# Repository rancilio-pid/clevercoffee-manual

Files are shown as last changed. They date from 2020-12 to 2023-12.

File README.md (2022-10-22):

# CleverCoffee Manual

## Über
Dies ist das Handbuch für die Umsetzung des CleverCoffee-Projektes. Dieses Handbuch deckt alle notwendigen Schritte ab. Dazu gehören zum einen die Installation von PlatformIO und das Hochladen auf den Mikrocontroller. Weiterhin beinhaltet das Handbuch die Bestellliste, Infos zum Einbau und der Konfiguration der PID-Parameter.

Hier geht es zum deutschen Handbuch: [Link](https://manual.rancilio-pid.de/de/).

Mehr zum Projekt findet ihr auf der [Clever Coffee Website](http://clevercoffee.de/).

## About

This is the manual for the implementation of the CleverCoffee project. This manual covers all the necessary steps. This includes installing PlatformIO and uploading the code to the microcontroller. The manual also includes the parts list, information on installing and configuring the PID parameters.

Click here for the English manual: [Link](https://manual.rancilio-pid.de/en/)

You can find more about the project on the [Clever Coffee Website](http://clevercoffee.de/).

## Contributing

Bug reports and pull requests are welcome on GitHub at [https://github.com/rancilio-pid/ranciliopid-handbook](https://github.com/rancilio-pid/ranciliopid-handbook).

This project is intended to be a safe, welcoming space for collaboration, and contributors are expected to adhere to the [Contributor Covenant](https://www.contributor-covenant.org/) code of conduct.

### Design and development principles of this manual:

* As few dependencies as possible
* As few (jekyll) customization as possible

## License
This manual is available as open source under the terms of the [MIT License](./LICENSE).

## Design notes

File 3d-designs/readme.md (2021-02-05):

Tipps zum Drucken:

1. Gehäuse auf dem Kopf liegend drucken (um 180° in X oder Y drehen)
2. Ein halbwegs Temperaturstabiles Filament verwenden (normales PLA ist etwas knapp)
3. Optimiert für eine 0,4mm Düse und eine Schichthöhe von 0,2mm
4. Für einen schönen optischen Touch in der ersten Schicht conzentrischen Infill verwenden

Die Magneten mit 6mm Durchmesser (2x 1mm und 1x 2mm dick) mit einem guten Kleber einkleben - Sekundenkleber hat sich als ungeeignet herausgestellt. 

Nach der [Einbauanleitung.pdf](./Einbauanleitung.pdf) zusammenbauen und montieren.

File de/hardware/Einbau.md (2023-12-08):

---
layout: default
title: Einbau
parent: Hardware
grand_parent: DE - Handbuch
has_children: false
nav_order: 3
---

#   {{ page.title }}

<details open markdown="block">
  <summary>
    Inhaltsverzeichnis
  </summary>
  {: .text-delta }
1. TOC
{:toc}
</details>

Grundsätzlich würde ich alle Kabel erstmal mit einer Kabellänge von ca. 60 cm abschneiden. Nach dem Einbau auf Seite 1 und dem Verlegen sollten diese beim Anschließen an Seite 2 gekürzt werden.

Vorbereitung:
* ESP bespielen (ggf. sicherstellen, dass das WLAN funktioniert)
* PCB zusammenlöten (Link zur Anleitung folgt)
* ggf. Blynk einrichten und verbinden
* ggf. Displayhalter drucken / bestellen

Zeitaufwand:
* PID Only ca. 3 h
* Vollaubau weitere 2-3 h

## Zerlegen

Als erstes muss die Maschine zerlegt werden. Hier findet ihr einen [Link zur Demontage](https://clevercoffee.de/rancilio-silvia-demontage/).

## PID only

### Thermostat gegen Temperatursensor tauschen

Kabel (0,14mm2) am Temperatursensor anlöten und mit Schrumpfschlauch versehen. **!!!Unbedingt Pinbelegung beachten!!!** Es empfiehlt sich folgende Belegung zu verwenden:

> Rot = +  
> Schwarz = -  
> Grüne = Signal

Freies Kabelende beschriften

Stecker mit rotem Kabel und Stecker mit grauem Kabel abziehen.

Schrauben 1 + 2 lösen.
Schraube 3 ein wenig lockern.
Das alte Thermostat beiseite legen und aufheben; bereich von der Wärmeleitpaste reinigen.

Bügel mit Schraube, Beilagscheiben und Muttern vorbereiten. Bügel wieder einbauen dabei Schraube 3 und 2 festziehen, 1 noch etwas locker lassen.

Die neue Schraube mit Hilfe der zwei Muttern so einstellen, dass die Schraube auf dem Temperatursensor aufliegt. Muttern festziehen.
Temperatursensor auf der Unterseite mit etwas Wärmeleitpaste versehen, unter der neuen Schraube platzieren und Schraube 1 anziehen. Der Bügel sollte sich dabei leicht verformen. So wird sichergestellt, dass der Sensor fest sitzt, aber nicht zu sehr gequetscht wird.  

### Stromversorgung

1,5mm2 Kabel blau mit Flachsteckhülse mit Abzweig versehen und in den abgezogenen Stecker mit Rotem Kabel stecken.
Ein weiteres 1,5mm2 Kabel blau mit Flachstecker versehen und ebenfalls einstecken. Alles mit einem Schrumpfschlauch versehen.
Kabel eins geht zum SSR der Heizung, Kabel zwei zum Netzteil. Welches Kabel dabei wofür verwendet wird ist egal.

1,5mm2 Kabel schwarz mit Flachsteckhülse mit Abzweig versehen. Den unteren Stecke am Schutzschalter abziehen, auf den Abzweig stecken und beides direkt wieder anstecken.

Kabel sinnvoll verlegen und einen Platz für das Netzteil festlegen. Kabel vor dem anschließen entsprechend kürzen.

Wenn man das Netzteil aus der Bestellliste nimmt, verbindet man Eingang N blau mit blau und Eingang L schwarz mit braun.
Der Ausgang von Netzteil schwarz-rot kommt dann auf den V_IN 5V Eingang am PCB.

### SSR Relais Heizung

Montagepunkt für das SSR festlegen. Es kann bei der Rancilio Silvia E z.B. über der "CPU" neben dem Wasserschlauch mit doppelseitigem Klebeband angebracht werden. Alternativ befindet sich eine Schraube an der Vorderseite der Maschine (hinter der Abdeckung), auf die das SSR mit einer Mutter festgeschraubt werden kann.

An Kabel 2 (blau) des Schrittes oben, eine Ringöse pressen (Kabel vor dem Anschließen entsprechend kürzen) und an einen beliebigen Pol des SSR-Ausgangs anschließen.
Ein weiteres Kabel 1,5 mm2 mit einer Ringöse versehen und am zweiten Pol des SSR-Ausgangs befestigen. Kabel zum Stecker mit dem grauen Kabel verlegen, welches ursprünglich am Thermostat war und entsprechend kürzen. Einen Flachstecker aufpressen und anschließend mit einem Schrumpfschlauch versehen.

Zwei Kabel (rot und schwarz) an der Eingangsseite des SSR anschließen. Ich habe dafür 0,5 mm2 Kabel verwendet und ebenfals Ringösen aufgepresst. Es können aber auch die 0,14 mm2 Kabel mit Aderendhülsen o.ä. verwendet werden.
Freie Kabelenden beschriften und richtung 3-Wegeventil legen.

### Einbau des Controllers

Der Microcontroller (ESP) sollte auf das von uns bereitsgestellte Adapterboard (PCB) gesteckt werden. Dieses kommt mit Klebefüßen, so dass es an einer beliebigen günstigen Position befestigt werden kann, an der die Kabel zusammenlaufen. Dies kann im hinteren oder vorderen Teil der Maschine sein, je nach Modell.

## Vollausbau

**Wichtig!: Beim anschließen des Brühschalters bitte unbedingt den Hinweis im Schaltplan zur Trennung von 230V und 3.3/5V am Schalter beachten.** (Wer der Anleitung unten folgt, muss nichts "zusätzlich" beachten.)

### Silvia (v2)

Beim Vollausbau werden sowohl Kaffebezug (inklusive 3-Wege-Ventil) und Dampfbezug über den ESP gesteuert. 
Dazu gibt es grob drei Arbeitsschritte, die unten genauer ausgeführt werden.
1. Schalter auf LED umrüsten
2. Pumpe anschließen
3. Magnetventil anschließen

#### Schalter Umrüsten

Es müssen sowohl der Schalter für Kaffebezug als auch für den Dampf auf LED umgerüstet werden. 
Dazu dieser Anleitung folgen: [LED-Umbau der Schalter](LED_Umbau.md)

Da direkt beide Schalter umgebaut werden, bietet es sich an, je ein gemeinsames Kabel für 3.3V und GND zu ziehen und dieses vom ersten zum zweiten Schalter durchzuschleifen. Inklusive der beiden Signalleitungen braucht es dann nur vier statt sechs Kabel quer durch die Maschine. 

#### Magnetventil anschließen 

1. Vom Hauptschalter L (schwarz) ein Kabel zum Relais für Pumpe und Ventil ziehen. Dieses Kabel werden sich Pumpe und Ventil teilen. Am Ende beim Relais also z.B. eine Wago-Klemme für drei Kabel oder einen Steckverbinder mit Abzweig anbringen. 
2. Weiteres (kurzes) Kabel von Wago/Steckverbinder zu "SW1" auf der 220V-Seite des Relais legen. 
3. Am zweiten Anschluss von SW1 am Relais ein Kabel anschließen. Kabel so ablängen, dass es zum Ventil führt. Steckverbinder anbringen, orangenes Kabel am Ventil abziehen, stattdessen neues Kabel aufstecken. 
4. Weiteres Kabel N (rot) zum Ventil legen und auf den Stecker mit vormals weißem Kabel aufstecken. Ich habe den Strom beim neuen Netzteil für den ESP abgegriffen, im Prinzip eignet sich aber jedes in der Nähe liegende Kabel mit N (rot) vom Hauptschalter. 
5. Kabel für 5V, GND und VALVE vom ESP zum Relais legen. (Wenn Dupont-Stecker am ESP verwendet werden, bietet es sich an, direkt auch die Leitung für das Pumpen-Signal mit anzubringen). Am Relais darauf achten, dass das die Steuersignal korrekt anliegen (wenn Ventil wie oben an SW1 angeschlossen, dann Signal für Ventil an CH1). 
6. Software konfigurieren, flashen, Maschine mit dem Strom verbinden, Bezug testen -- das Ventil sollte deutlich hörbar klacken, wenn der Bezugschalter umgelegt wird. 
7. Vor dem Weitermachen Maschine vom Strom trennen.

#### Pumpe anschließen

1. Ein zweites (kurzes) Kabel von Wago/Steckverbinder aus Schritt 1 des Ventil-Anschlusses zu "SW2" auf der 220V-Seite des Relais legen. 
3. Am zweiten Anschluss von SW2 am Relais ein Kabel anschließen. Kabel so ablängen, dass es zur Pumpe führt und einen Steckverbinder mit Abzweig anbringen. Das weiße Kabel an der Pumpe abziehen, auf den Abzweig des neuen Kabels stecken, und gemeinsam wieder an der Pumpe anbringen. 
4. Wenn nicht beim Anschluss des Ventils schon erledigt, Kabel für das Steuersignal der Pumpe vom ESP zum Relais legen (wenn Pumpe wie hier beschrieben an SW2 angeschlossen, dann Signal für Pumpe an CH2). 
5. Maschine an Strom anschließen, Bezug testen. 
5.1. Wenn alles funktioniert: Glückwunsch, Vollausbau abgeschlossen! 
5.2. Wenn die Pumpe nichts tut: Vermutlich schaltet dein Relais nur beim Nulldurchgang (mehr Info hier: [Bestellliste](../bestellliste.md)). Um das zu testen, einen 100k Ohm Widerstand (Leistung 1 Watt, bitte weitere Hinweise in der Bestellliste beachten) parallel zur Pumpe anschließen. Ich habe dazu beide Kabel an der Pumpe abgezogen und die Stecker abgeknippst. Dann neue Stecker anbringen und dabei zusätzlich zum Kabel jeweils ein Beinchen des Widerstands mit verpressen. Danach müssen die Kabel vorsichtig (und gemeinsam) angebracht bzw. abgenommen werden, da sie jetzt durch den Widerstand verbunden sind. Zum Abschluss noch einmal Bezug testen und den Vollausbau genießen! 

## Display

Es gibt unzählig viele Möglichkeiten das Display zu positionieren. Folgend könnt ihr zwei Beispiele sehen:

Displayhalterung | Powered by Dremel
:---:|:---:
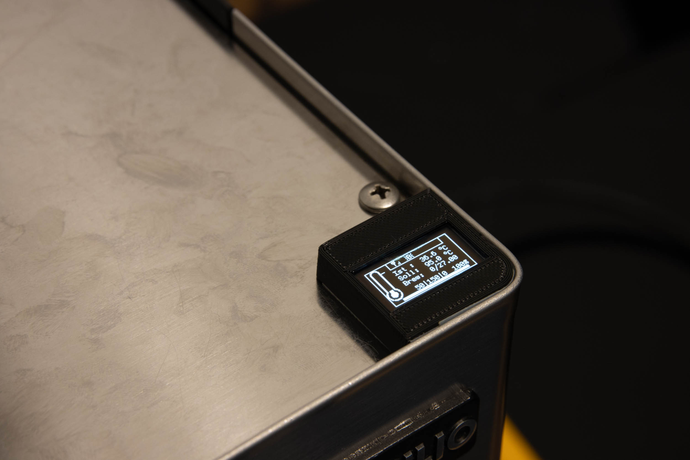
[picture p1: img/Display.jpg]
Display
|

Wer einen Dremel besitzt, etwas Geschick mitbringt und kein Problem damit hat, dass Änderungen irreversibel sind, kann damit eine sehr saubere und solide Lösung ausarbeiten.

Wer hintgegen eine reversible Lösung sucht muss sich um eine Displayhalterung (aka 3D Case) bemühen. Eine "Standardlösung" ist aktuell nicht bekannt, aber für alle 3D-Drucker Besitzer, liegen entsprechende Vorlagen auf [Github](https://github.com/rancilio-pid/ranciliopid-handbook/tree/main/3d-designs) (inkl. [Anleitung](https://github.com/rancilio-pid/ranciliopid-handbook/blob/main/3d-designs/Einbauanleitung.pdf) für den Einbau und die Magnete):

* [Rancilio STL](https://github.com/rancilio-pid/ranciliopid-handbook/blob/main/3d-designs/Case%20Rancilio.stl){:target="_blank"}
* [Gaggia STL](https://github.com/rancilio-pid/ranciliopid-handbook/blob/main/3d-designs/Case%20Gaggia.stl){:target="_blank"}
* [Universal-Halter](https://www.thingiverse.com/thing:4897546){:target="_blank"}
* [Halterung zum reinklicken](https://www.thingiverse.com/thing:4662947){:target="_blank"}

## Spannende Addons die gleich mit erledigt werden können

* Senkschraube am Sieb
* Reinigung der Wasserschläuche (sofern die Maschine nicht neu ist)
* [LED-Umbau der Schalter](LED_Umbau.md)

## Ausblick

Features die ebenfalls eingebaut werden können:

* digitales Manometer
* [integrierte Waage](Waage.md)
* Silvia E Zeit für automatisches Ausschalten verändern
* Automatische Funktion zum Wechsel von Dampf auf Brühen

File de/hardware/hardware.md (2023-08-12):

---
layout: default
title: Aufbau
parent: Hardware
grand_parent: DE - Handbuch
has_children: false
nav_order: 1
---

# Aufbau und Einbau der Hardware
{: .no_toc }

Inhaltsverzeichnis

* TOC
{:toc}

## Trockenaufbau

Wenn ihr die einzelnen Komponenten beisammenhabt, startet ihr am besten mit einem Trockenaufbau außerhalb eurer Maschine. So könnt ihr das System zum Laufen bringen und kommt jederzeit problemlos an alle Stecker etc. heran.

Die Heizung eurer Maschine könnt ihr z. B. mit einer Glühbirne simulieren, jeder andere 230V Verbraucher tut es aber genauso gut.

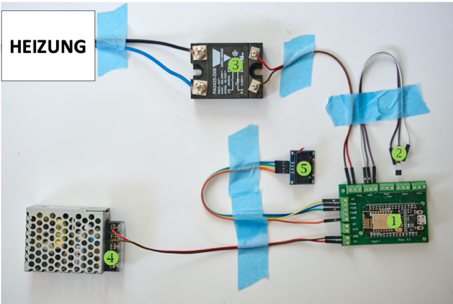
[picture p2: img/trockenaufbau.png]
Trockenaufbau


*(1=Mikrocontroller, 2=Temperatursensor, 3=SSR Relais für Heizung, 4=Schaltnetzteil, 5=Display)*

Das PCB für den (neuern) Mikrocontroller ESP32 sieht wie folgt aus:
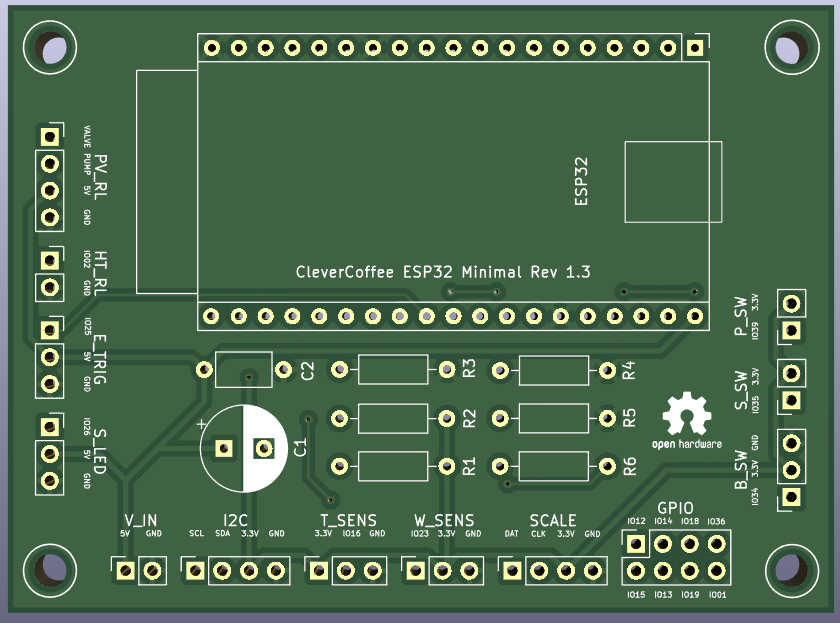
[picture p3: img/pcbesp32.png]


Das PCB für den (älteren) Mikrocontroller ESP8266 sieht wie folgt aus:

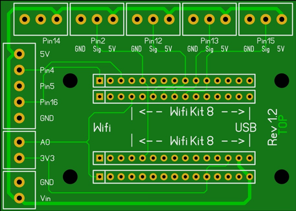
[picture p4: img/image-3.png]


##  PIN Belegung vom PCB ESP32

PIN Software | Bezeichnung auf dem PCB | Belegung
-|-|-
PIN 2 | HT_RL | SSR Heizung     
PIN 16 | T_SENS | Temperatursensor
PIN 21 | IC2 (SDA) | Display-PIN SDA
PIN 22 | IC2 (SDL) | Display-PIN SCL
GND/Vin | V_IN | Netzteil (5Volt)
PIN 17 | PV_RL (Valve) | Relais Ansteuerung Magnetventil
PIN 27 | PV_RL (Pump) | Relais Ansteuerung Pumpe
PIN 34 | B_SW | Bezugsschalter oder Optokopler 
PIN 35 | S_SW | Dampfschalter
PIN 39 | P_SW | Powerschalter (aktuell nicht in Software enthalten)
PIN 25 | E_TRIG | Anschluss Trigger Silvia E CPU
PIN 26 | S_LED | Status oder Temp LED
PIN 23 | W_SENS | Wasserstandssensor
PIN 32 | SCALE (DAT) | Waage DAT
PIN 33 | SCALE (CLK) | Waage CLK

##  PIN Belegung vom PCB ESP8266

Die einzelnen Komponenten werden wie folgt angeschlossen:

PIN | Belegung
-|-
PIN 14 | SSR Heizung     
PIN 2 | Temperatursensor
PIN 4 | Display-PIN SDA
PIN 5 | Display-PIN SCL
GND/Vin | Netzteil

### Vollausbau

Bei dem „Vollausbau“ wird noch die Steuerung für Magnetventil und Pumpe benötigt:

PIN | Belegung
-|-
PIN 12 | Relais Ansteuerung Magnetventil
PIN 13 | Relais Ansteuerung Pumpe

## Einbau

### Temperatursensor anschließen

**ACHTUNG!!** Aktuell kann es sein, dass der TSIC mit einem falschen Datenblatt ausgeliefert wird. Hier wird die Polung falsch angegeben.
Lest hierzu bitte folgenden Thread im Chat durch: [Link](https://chat.rancilio-pid.de/ranciliopid/pl/dcf38jzk3pnoig5hi64nuodeqc).

Besondere Sorgfalt müsst ihr bitte beim Anschließen des Temperatursensors TSIC 306 walten lassen: sobald dieser einmal falsch angeschlossen Spannung bekommen hat, ist er entweder sofort zerstört oder zumindest vorgeschädigt und liefert dadurch fehlerhafte Messwerte. Daher ist es immer ratsam einen Ersatz-Sensor parat zu haben.

* Sensor V+ : Board PIN 2 5V
* Sensor Signal: Board PIN 2 Signal
* Sensor GND:  Board PIN 2 GND

Wie ihr zu der Beschreibung zum Board sehen könnt, muss an Pin 2 der Temperatursensor angeschlossen werden. Die oberen Ports (14, 2, 12, 13, 15) sind einheitlich jeweils von links nach rechts mit Minus(-), Signal, 5V(+) belegt.

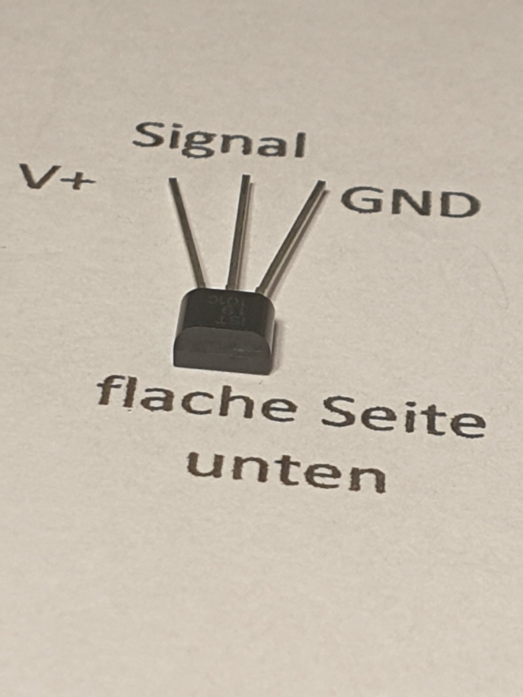
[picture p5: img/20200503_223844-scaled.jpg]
TSIC Sensor


Da wir öfters hören, dass die mitgelieferte Bildbeschreibung des TSIC nicht gut ist, haben wir hier nochmals die Pins vom Sensor dargestellt. Die flache Seite liegt unten. Ein falsch gepolter TSIC sollte entsorgt werden! Er misst vermeintlich richtig, aber definitiv nicht mehr genau.

Beim Anschließen des SSR zur Ansteuerung der Heizung ist es wichtig, dass die Polarität der SSR-Ports 3 und 4 beachtet werden:

* SSR Port 3 (+) : Board PIN 14 Signal
* SSR Port 4 (-) : Board PIN 14 GND

Damit habt ihr das System zum ersten Mal aufgebaut.

### PIN Belegung vom PCB

Pin|Funktion
-|-
Pin 12| Relay für das Ventil
Pin 13| Relay für die Pumpe
Pin 15| Schalter Brühtaste
Pin 14| Relay für die Heizung
Pin 2| Temperatursensor
A0| Drucksensor
|
Pin 4| SDA
Pin 5| SCL
Pin 16| E-Trigger Standby Trigger Silvia E

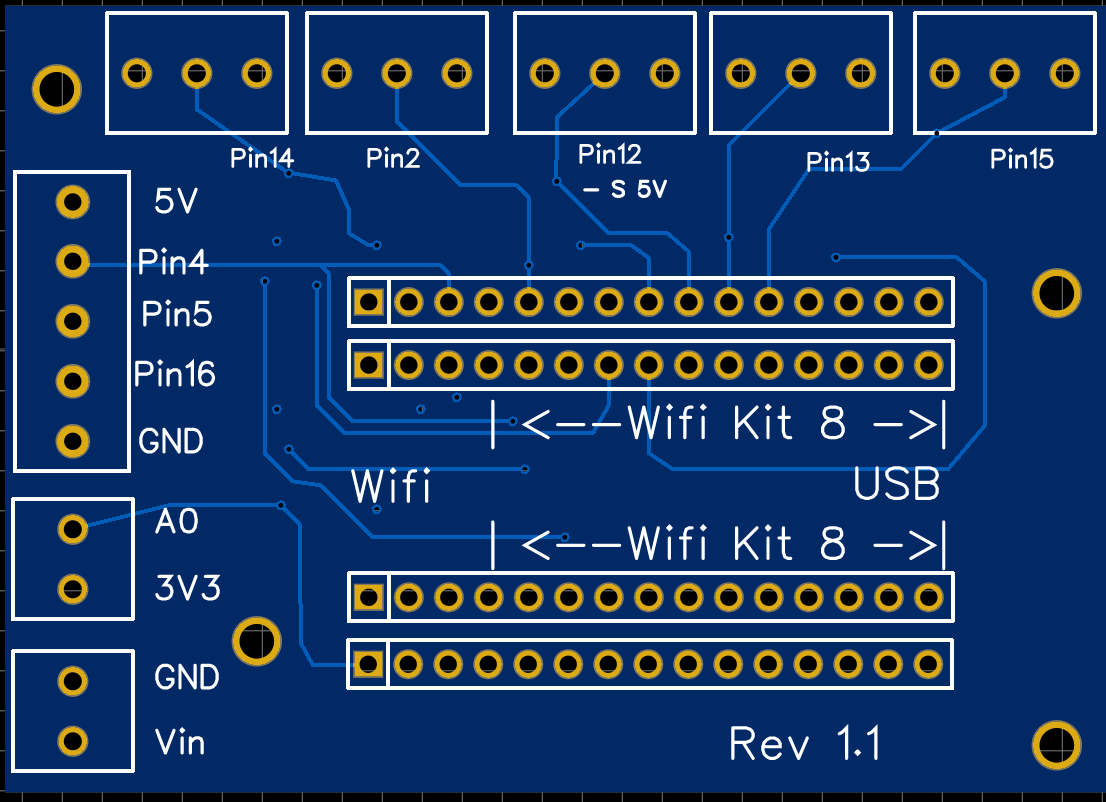
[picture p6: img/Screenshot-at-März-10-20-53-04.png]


## Tipps und Tricks

Hier einige gesammelte Hinweise zum Einbau in die Maschine:

* Verbaut die Komponenten an einem trockenen Ort und möglichst entfernt von der Hitzequelle Boiler.

* Das SSR schaltet die Heizleistung von ca. 1.000 W, von daher kann eine Montage mit wärmeleitendem Kleber bzw. Klebepads nicht schaden.

*  Den Temperatursensor solltet ihr wenn möglich nicht nur an den Kessel ankleben, sondern fest verschrauben. Bei der Rancilio Silvia kann man dazu die Halteklammer des nun überflüssigen Brühthermostaten nutzen, bei der Gaggia Classic kann der Sensor am vorhandenen M4-Gewinde der Thermostataufnahme verschraubt werden.

* Zum Anschluss des Temperatursensors TSIC keine Steckverbinder (Jumperkabel) nehmen, sondern Litze an die Beine des TSIC löten. Das ist etwas fummelig, aber dafür habt ihr weniger Neigung zu Wackelkontakten im verbauten Zustand.

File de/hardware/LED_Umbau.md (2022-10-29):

---
layout: default
title: LED-Umbau
parent: Hardware
grand_parent: DE - Handbuch
has_children: false
nav_order: 5
---

# LED-Umbau der Wippschalter
{: .no_toc }

Inhaltsverzeichnis

* TOC
{:toc}

## Warnhinweis

> {{ site.warnhinweis }}

## Einleitung
Wir möchten die Schalter von 230V auf 3.3V bzw. 5V umbauen um das Signal direkt ohne Optokopller o.ä. an den Mikrocontroller weitergeben zu können. Dies ist glücklicherweise recht einfach ohne Löten oder änhliches und vor allem reversibel möglich. Der größte Aufwand hierbei ist es, dass ein Teil der alten Verkabelung raus muss und die Schalter neu verdrahtet werden müssen, hierzu aber am Ende des Kapitels mehr. 

Was brauchen wir für den Umbau  
- Jeweils 1x LED der gewünschte Farbe in 5mm  
- Pro Schalter 2x Widerstände der Bauform SMD 0207 MELF

Als LEDs eignen sich für die Rancilio am besten LEDs in der Farbe Orange/Amber mit einer nicht all zu großen Helligkeit. Bisher als recht passend erwiesen haben sich diffuse LEDs mit einer Helligkeit im Bereich von 1800 mcd.   
Die Widerstände müssen passend zu der LED und der gewünschten Spannung ausgewählt werden (3.3V oder 5V).
Am einfachsen nimmt man hierfür einen LED-Widerstandsrechner wie z.B. folgenden:  
[https://www.leds-and-more.de/catalog/resistor.php]()  
Am Beispiel einer orangen LED mit einer Durchlassspannung von 1.8 V und einer Stromaufnahme von 20 mA bei einer Betriebsspannung von 3.3V ergibt dieser dann 75 Ohm. Bei den bisher verwendeten LEDs war das Licht durch den Schalter noch recht intensiv deshalb habe ich einfach den Widerstand verdoppelt. Wer sich nicht ganz sicher ist, besorgt sich am besten vorher die LEDs und testet mit nem handelsüblichen Widerstandssortiment oder Potis die Helligkeiten aus. Im Beispiel brauchen zu den LEDs pro Schalter 2 MELF Widerstände mit jeweils 75 Ohm. Das sieht dann wie folgt aus:

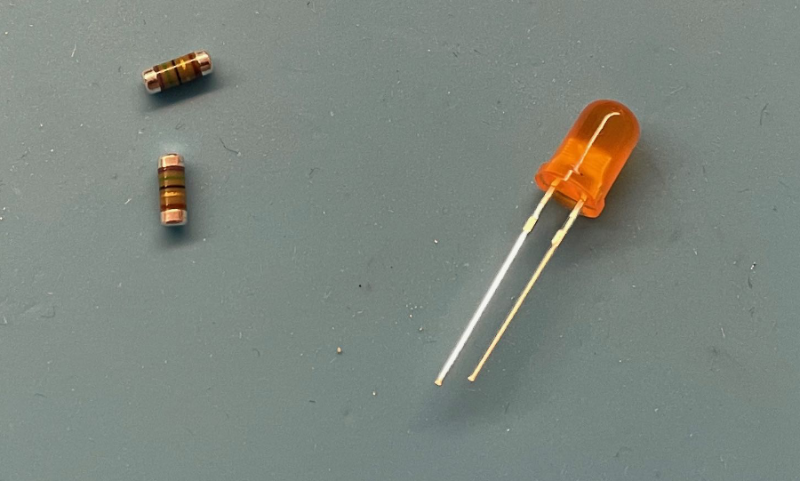
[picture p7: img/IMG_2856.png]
LED Komponenten


## Der Ausbau
Als erstes Maschine vom Netz trennen und nicht nur ausschalten! Dann erstmal alle Kabel von den umzubauenden Schaltern ab. Die Schalter werden jeweils oben und unten mit 2 Rastenasen im Gehäuse gehalten. Hier am besten von oben nach unten die Schalter der Reihe nach ausbauen. Mit den beiden oberen Nasen des ersten Schalters anfangen. Mit einem Schraubenzieher oder ähnlichem die Rastnasen nach unten drücke und den Schalter leicht nach vorne aus der Maschine kippen. Dann mit den Fingern oder irgendeinem passenden Werkzeug (Küchenutensilien zählen auch als Werkzeug) die beiden untere Rastnasen drücken. Das ganze ist bisschen fummelig, aber der Schalter lässt sich in der Regel langsam nach vorne rauswandern. 

Wenn wir nun den Schalter von uns haben nacheinander von beiden Seiten mit einem schmalen Schraubendreher die Kappe des Schalters nach vorne raushebeln. 
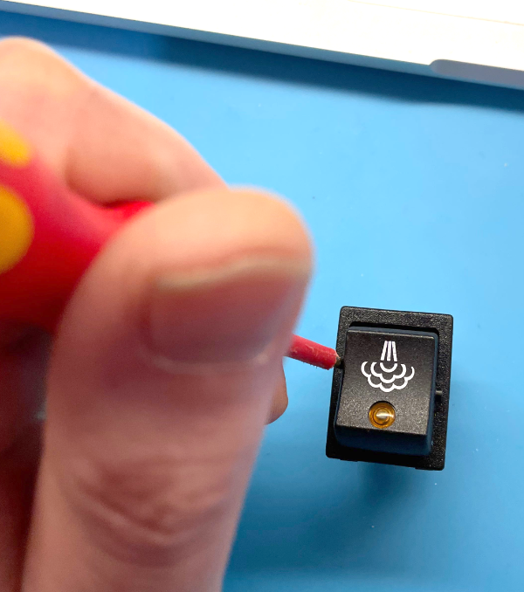
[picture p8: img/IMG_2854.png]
Aufhebeln


In dem Schalter finden wir die Schaltwippe selber mit einer 90V Neonsingalbirne, zwei Spiralfedern, zwei Widerstände und zwei Blattfedern unter der Schaltwippe. Die Widerstände sind von hinten unter den Spiralfedern versteckt und werden von diesen gehalten. Zum Zerlegen erst die Federn abziehen, dann die Widerstände raus, jetzt sollte die Birne schon fast von alleine herausfallen.  

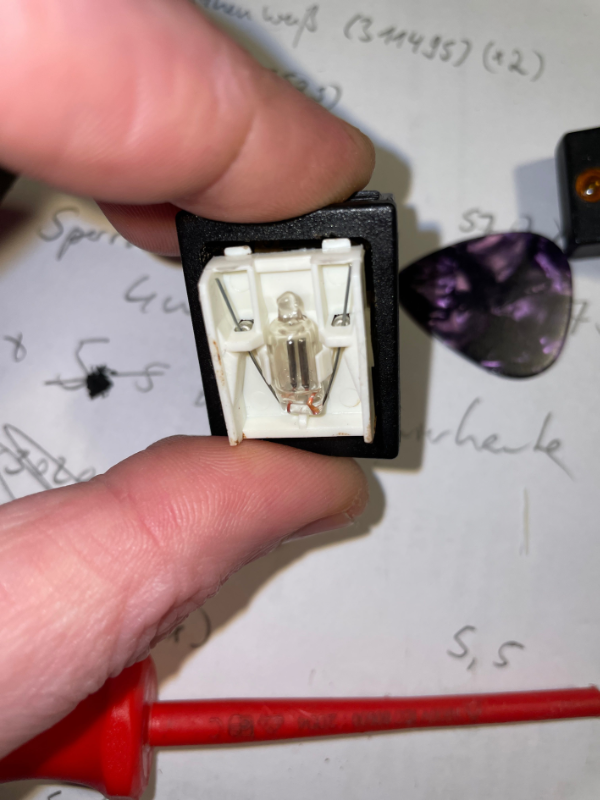
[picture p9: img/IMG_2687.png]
Innereien
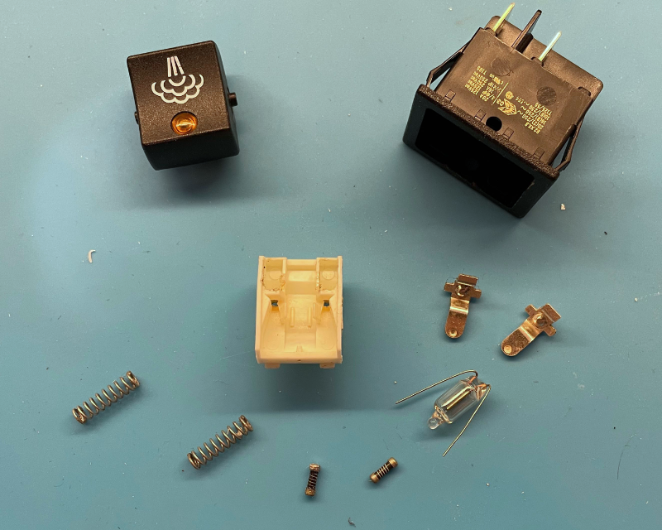
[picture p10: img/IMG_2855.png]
Ausgeweidet
 

Die Neonbirne und beide Widerstände tüten wir ein und legen sie beiseite falls die Schalter irgendwann mal wieder zurück gebaut werden sollten. 

## Zusammenbau
Jetzt geht es auch schon wieder an den Zusammenbau. Beim Einbau der LED daran denken, dass diese eine Durchflussrichtung hat. Wenn wir von vorne auf den Schalter schauen möchten wir die Anode (+) der LED auf der rechten Seite haben. Die positive Seite der LED erkennt man daran, dass diese ein längeres Beinchen besitzt. Zudem ist die negative Seite der LED meistens am Kunstoff abgeflacht. 
Da die Beinchen der 90V Glühlampe bisschen dicker sind als die einer LED und in meinem Fall auch die Widerstände minimal kürzer, empfiehlt es sich die Beine der LED einmal zu falten. Damit kann der Dickenunterschied einfach überbrückt werden.

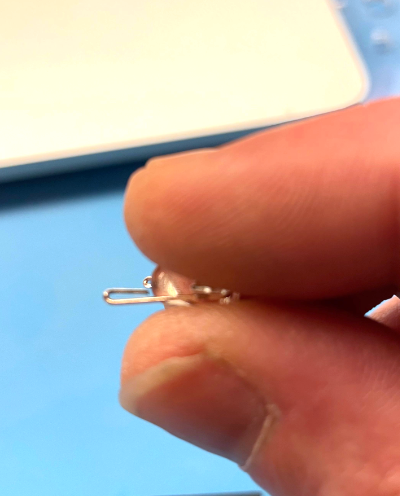
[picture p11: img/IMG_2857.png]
BeinchenBieger3000


Wer an dieser Stelle z.B. den Brühschalter zu einem Taster umbauen möchte, der kann an dieser Stelle einen alten Kugelschreiber opfern. Einfach die Kugelschreiberfeder in das Loch in dem Schaltergehäuse stecken. Je nach Feder diese eventuell noch kürzen. 

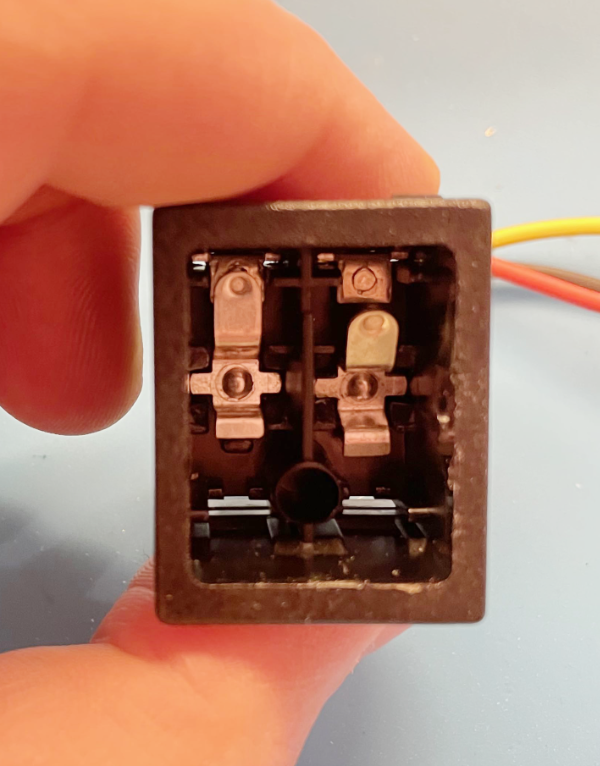
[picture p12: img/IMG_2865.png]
Federaufnameloch


Den Schalter jetzt in umgekerter Reihenfolge wieder zusammenbauen. Am Ende sollte es so aussehen. 

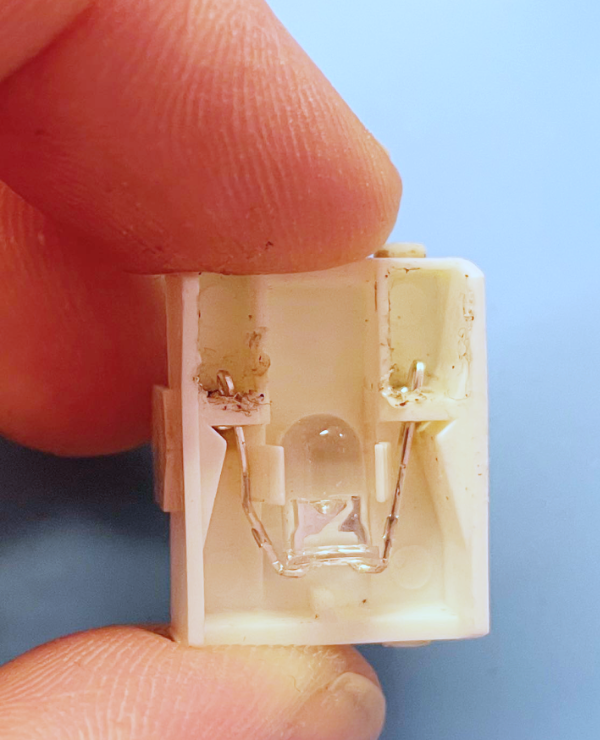
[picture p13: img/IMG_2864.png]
Zusammenbau


Wenn alle Schalter umgebaut sind können diese wieder in die Maschine eingesetzt werden. Als nächstes folgt dann die Verkabelung.

## Verkabelung

An dieser Stelle folgen später noch Schaltpläne je nach Ausbauart. Fürs erste gibts nur eine kurze Textbeschreibung für den Anschluss der Schalter als High-Trigger, also positiv schaltend.  
Auf der Rückseite der Schalter befinden Nummern für die Anschlüsse von 1-6, wobei hier nur die Anschlüsse 1,2,4,5 wirklich belegt sind. Vorrausgesetzt die LED wurde so wie oben beschrieben eingebaut, sieht die Belegung wie folgt aus:  

- VCC auf 1
- Signal auf 2
- GND auf 4

Wobei sich alle Schalter auch VCC und GND teilen können und Signal geht dann jeweils von dem Schalter zu den jeweiligen Eingängen auf dem Board. Da die meisten von euch, gerade beim ESP, nicht mehr genügend Eingänge frei haben werden um alle Schalter anzuschließen, kann z.B. der Wasserbezugschalter direkt mit an den Eingang des Relais für die Pumpe angeschlossen werden. In diesem Fall geht dann der Signal Ausgang (2) vom Schalter mit auf den Schalteingang des Reilais. Zur Zeit wird das im PID mit dem Signal des Wasserbezugs sowieso keine Funktion ausgelöst.
Hier noch ein Bild des fertig verdrahteten Schalters.
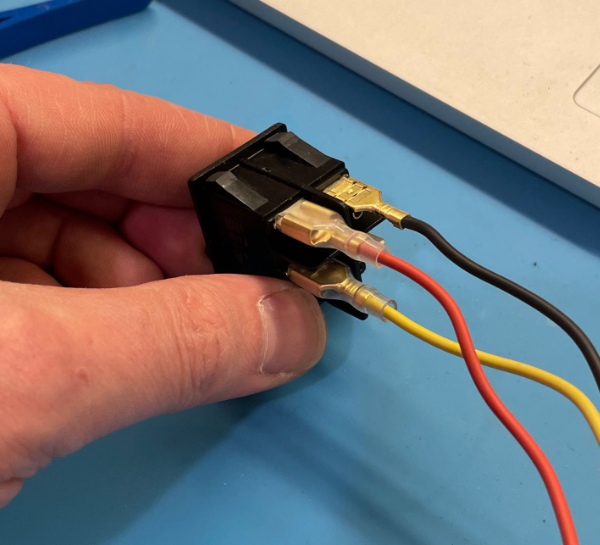
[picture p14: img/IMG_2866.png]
LeFin
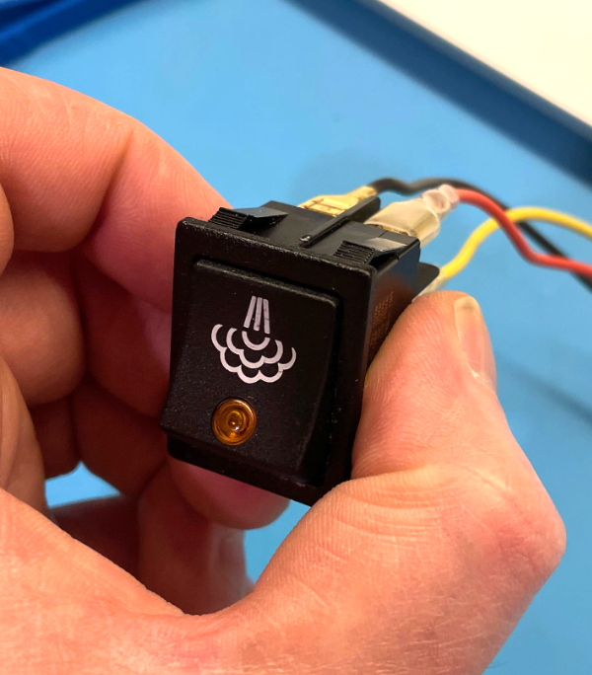
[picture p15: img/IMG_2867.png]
LeFin2


## To be continued
Als nächste wollte ich versuchen die LEDs der Schalter unabhängig vom Schaltzustand anzusteuern. Da hierfür nicht genügend Ausgänge auf den Boards frei sind werde ich mit einer Erweiterungsplatine experimentieren. Bei Rückfragen einfach im Chat fragen oder sich dort direkt an mich @derchristian wenden.

Erstellt am 18.05.2021 von Christian (@derchristian)  
zuletzt geändert am 18.05.2021 von Christian (@derchristian)

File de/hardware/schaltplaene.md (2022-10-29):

---
layout: default
title: Schaltpläne
parent: Hardware
grand_parent: DE - Handbuch
has_children: false
nav_order: 2
---

# Schaltpläne
{: .no_toc }

Inhaltsverzeichnis

* TOC
{:toc}

## Warnhinweis

> {{ site.warnhinweis }}

## Einleitung

Wenn der Test erfolgreich war, kannst du beginnen deinen Einbau zu planen. Je nach Ausbaustufe musst du nur das Netzteil und Controller mit Strom versorgen, den Temperatursensor einbauen am Kessel. Wir zeigen dir hier am Beispiel der Rancilio Siliva wie der Umbau gelingt. Weiter Maschinen, wie z.B. die Gaggia wurde auch schon erfolgreich umgebaut.

## Rancilio

### Originaler Schaltplan 

Der erste Schaltplan zeigt den original Zustand der Silvia vor dem Umbau.

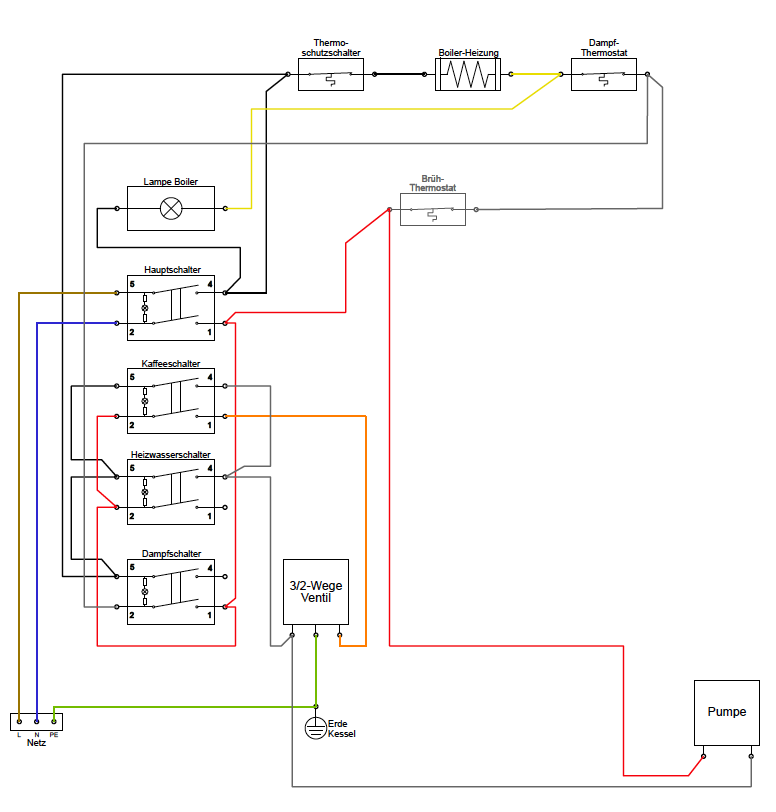
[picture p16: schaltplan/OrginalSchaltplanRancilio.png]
Org Schaltplan


### "Only PID"

Der zweite Schaltplan zeigt die PID Anpassung.
Diese Version ist nur für die Temperatursteuerung verantwortlich.
Die Pumpe und das 3-Wege-Ventil werden nicht durch den Controller gesteuert.

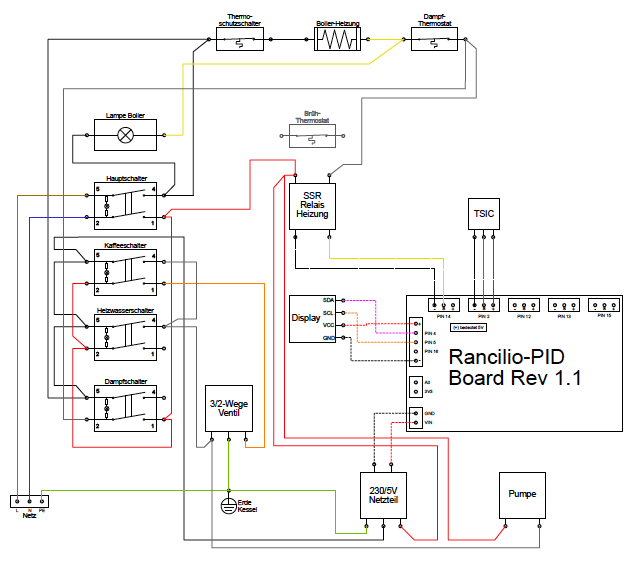
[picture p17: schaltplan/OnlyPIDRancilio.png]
PID Schaltplan


### "Only PID+"

Ein Schaltplan für Only PID+, also mit Optokoppler zur Brüherkennung liegt bisher noch nicht vor. Zusätzlich zum obigen Schaltplan ist ein Optoppler parallel zum Bezugsschalter und dem 3/2-Wegeventil zu setzen.

### "Vollausbau"

Der dritte Schaltplan ist der aktuelle „Vollausbau“.
Enthalten ist die PID für die Kesseltemperatursteuerung
Zusätzlich kann auch die Brühzeit oder eine „Preinfussion“ gesteuert werden. (Vorlauf-Brühzeit, Pause, Brühzeit).
Dabei werden Pumpe und das 3-Wege-Ventil vom Controller gesteuert.

**WICHTIGER HINWEIS: Dieser Umbau darf nur am Brüh-Schalter vorgenommen werden, wenn ein Schalter ohne Lampe genommen oder die Lampe ausgebaut oder eine neue Verkabelung bzw. der LED-Umbau gewählt wird, dass mit eingebauter Lampe KEINE 3,3 Volt und 230 Volt am Schalter anliegen! Sonst liegt KEINE galavanische Trennung zwischen 3,3 Volt und 230 Volt mehr vor! Das kann unter ungünstigen Umständen gefährlich für dich oder den Microcontroller sein!**

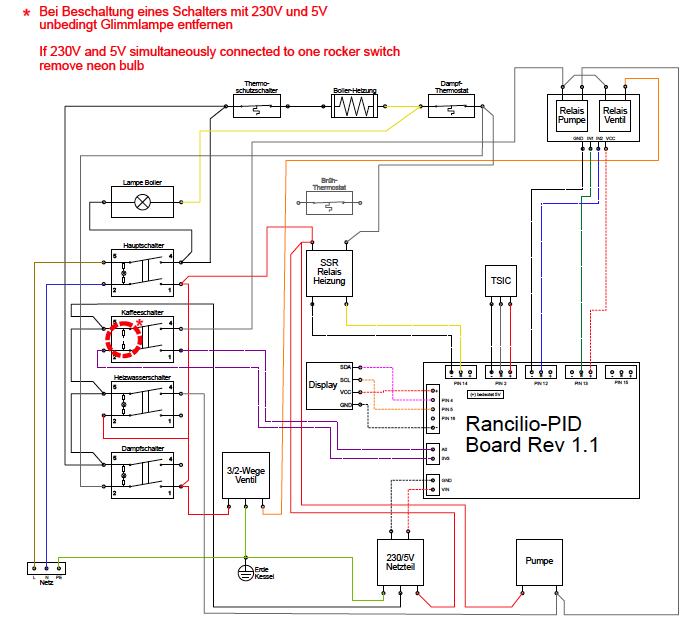
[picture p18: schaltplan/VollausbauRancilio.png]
Vollausbau Schaltplan


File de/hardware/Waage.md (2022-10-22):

---
layout: default
title: Waageneinbau
parent: Hardware
grand_parent: DE - Handbuch
has_children: false
nav_order: 4
---

# Aufbau und Einbau der Waage
{: .no_toc }

Inhaltsverzeichnis

* TOC
{:toc}

## Einführung

Für den Vollausbau besteht die Möglichkeit der Ergänzung einer Waage für den Bezug nach Gewicht (Stopp bei Zielgewicht).
Der Grundaufbau entspricht dabei bekannter Waagen mit einer Wägezelle. Diese wird mittels eines HX711 an den Arduino angeschlossen.
Einen ausführlichen Einblick bekommt ihr auch im Chat im Kanal Waage: [Link](https://chat.rancilio-pid.de/ranciliopid/channels/projekt-waage)

## Der Hardware-Aufbau

Ihr benötigt eine Wäägezelle mit einer ausreichend genauen Auflösung (0,1gr) und ausreichend Tragkraft (also größer Gewicht Abtropfschale + Lieblingstasse).
Aktuell sind folgende Zellen die meistverbauten: [Link] (https://amzn.to/2RWJnKs)

Um die Zellen am Gehäuse zu montieren gibt es eine Adapter-Lösung zum Klemmen, und eine zum Schieben, für den 3D-Drucker. Hier könnt ihr im Chat je nach Maschine die passenden Files finden.
Kanal Waage: [Link](https://chat.rancilio-pid.de/ranciliopid/channels/projekt-waage)

Anschließend verbindet ihr die Zellen mit dem HX711 und diesen mit den geeigneten freien Pins am Arduino.

Bild vom Einbau:

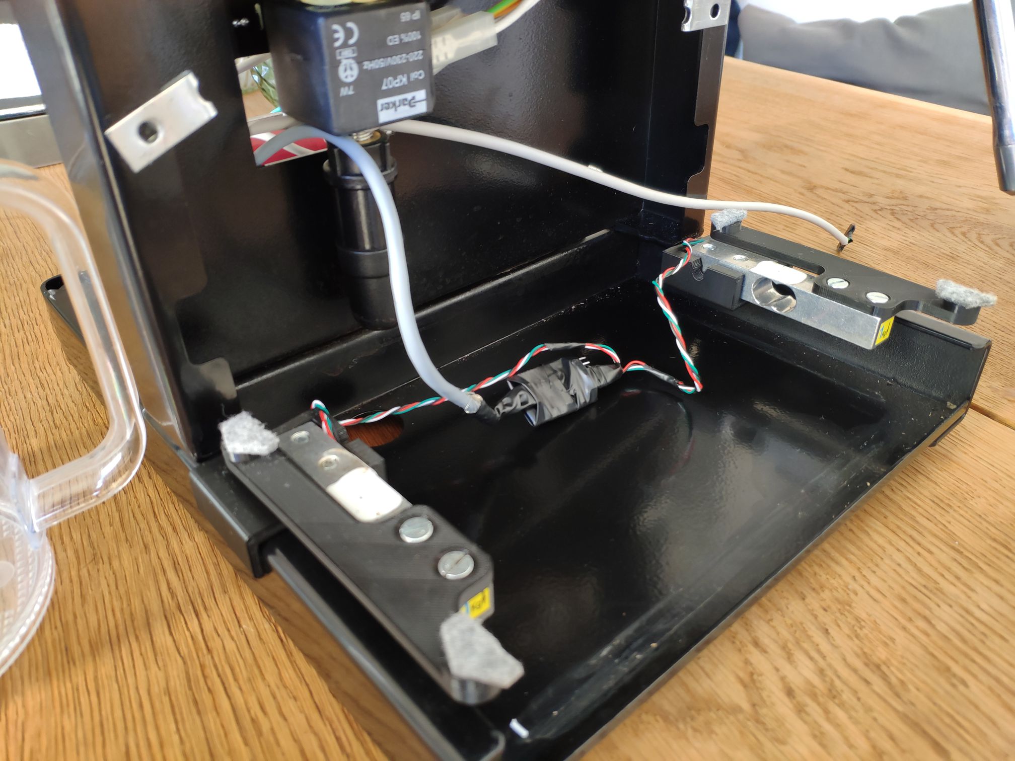
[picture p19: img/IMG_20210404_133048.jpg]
Waage


## Software

Vor dem Benutzen der Waage steht die Kalibrierung. Diese wird mit dem File in der HX711-Library durchgeführt. Dazu verkabelt ihr euren Waagen-Aufbau fertig, installiert die Tropfschale und steckt den Arduino per USB an.
Anschließend startet ihr die calibration.ino und führt die Kalibrierung wie beschrieben aus (auf Serial Port mit Bautrate 57600). Haltet dazu ein Kalibriergewicht parat, bei welchem euch das Gewicht bekannt ist, und das eurer Lieblingstasse mit Shot nahe kommt.
Tragt den Kalibrierungswert dann in die brewscaleini.h ein.
Ihr müsst nun noch euer PIN-layout sowie den "Scale"-modus in der Config nach eurem Setup eintragen.

## Shot nach Zielgewicht

In Blynk habt ihr im Bereich "Vollausbau" nun die Möglichkeit, neben dem Bezug nach Zeit, auch den Bezug nach Gewicht einzustellen.
Tipp: Da der Bezug entweder beim Erreichen der Zielzeit oder dem Zielgewicht stoppt, solltet ihr je nach gewünschtem Modus den anderen Wert auf einen nicht zu erreichenden Wert einstellen.
(z.B. Zielgewicht Shot = 48 gr. -> "Brühzeit"= 99 sek.)

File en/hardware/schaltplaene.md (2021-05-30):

---
layout: default
title: Schaltpläne
parent: Hardware
grand_parent: EN - Manual
has_children: false
nav_order: 2
---

# Schaltpläne
{: .no_toc }

Inhaltsverzeichnis

* TOC
{:toc}

## Warnhinweis

> {{ site.warnhinweis }}

## Einleitung

Wenn der Test erfolgreich war, kannst du beginnen deinen Einbau zu planen. Je nach Ausbaustufe musst du nur das Netzteil und Controller mit Strom versorgen, den Temperatursensor einbauen am Kessel. Wir zeigen dir hier am Beispiel der Rancilio Siliva wie der Umbau gelingt. Weiter Maschinen, wie z.B. die Gaggia wurde auch schon erfolgreich umgebaut.

## Originaler Schaltplan

Der erste Schaltplan zeigt den original Zustand der Silvia vor dem Umbau.

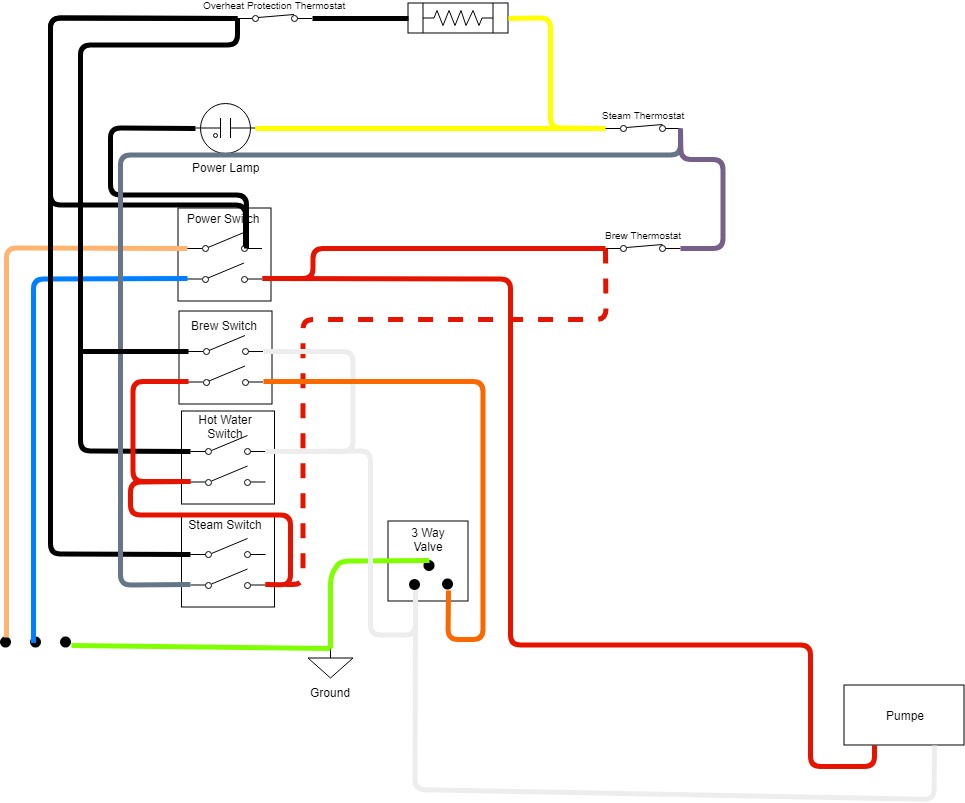
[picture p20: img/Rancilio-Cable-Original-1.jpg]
Org Schaltplan


## "PID Only"

Der zweite Schaltplan zeigt die PID Anpassung.
Diese Version ist nur für die Temperatursteuerung verantwortlich.
Die Pumpe und das 3-Wege-Ventil werden nicht durch den Controller gesteuert.

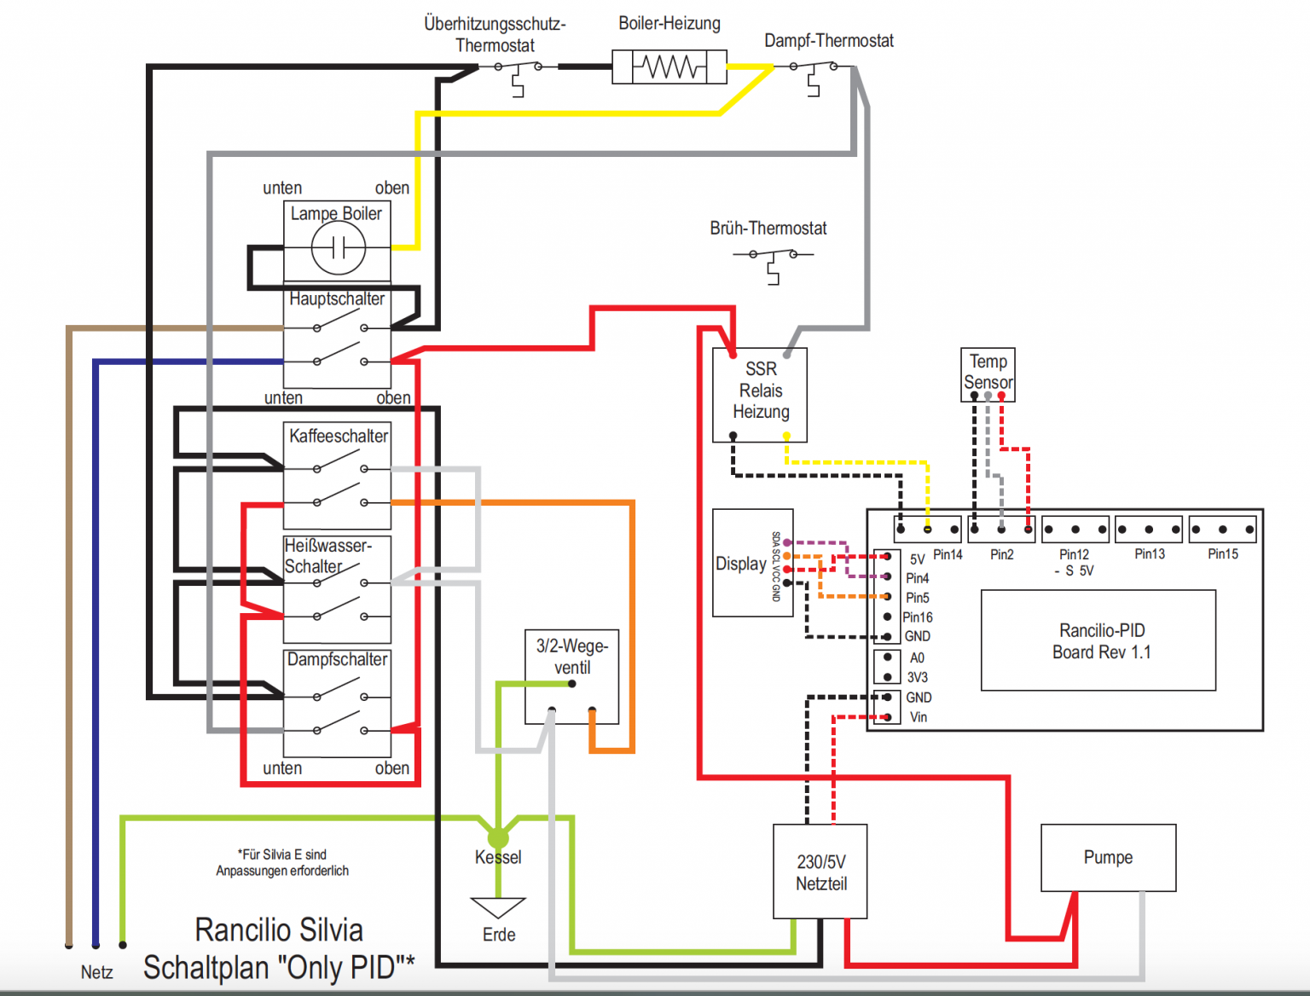
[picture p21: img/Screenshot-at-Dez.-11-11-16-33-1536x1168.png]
PID Schaltplan


## "Vollausbau"

Der dritte Schaltplan ist der aktuelle „Vollausbau“.
Enthalten ist die PID für die Kesseltemperatursteuerung
Zusätzlich kann auch die Brühzeit oder eine „Preinfussion“ gesteuert werden. (Vorlauf-Brühzeit, Pause, Brühzeit).
Dabei werden Pumpe und das 3-Wege-Ventil vom Controller gesteuert.

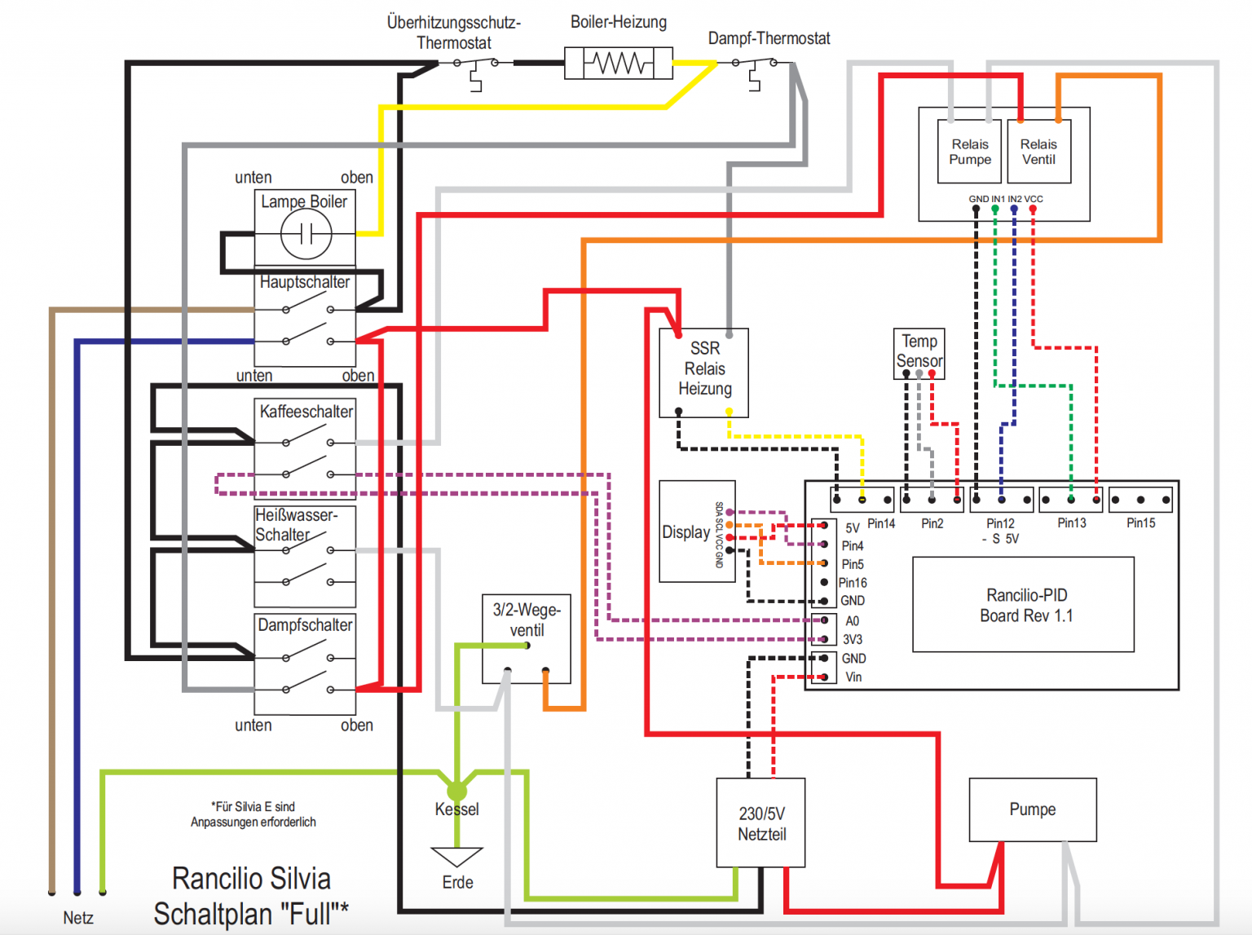
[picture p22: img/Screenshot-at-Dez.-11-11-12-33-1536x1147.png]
Vollausbau Schaltplan


## Schematische Darstellung der Ausgänge der Platine ESPresso Rev 1

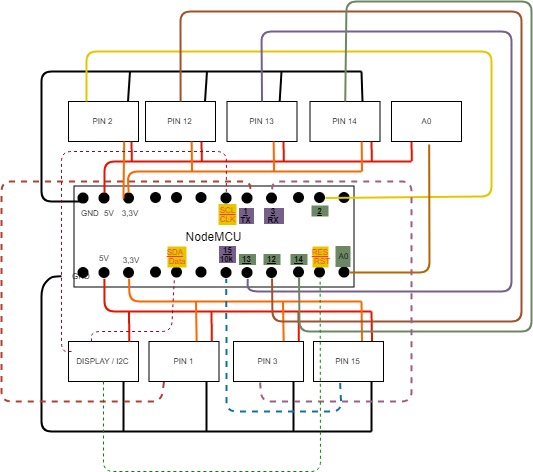
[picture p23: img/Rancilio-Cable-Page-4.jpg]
Platine Schaltplan


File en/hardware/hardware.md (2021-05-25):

---
layout: default
title: Aufbau
parent: Hardware
grand_parent: EN - Manual
has_children: false
nav_order: 1
---

# Aufbau und Einbau der Hardware
{: .no_toc }

Inhaltsverzeichnis

* TOC
{:toc}

## Trockenaufbau

Wenn ihr die einzelnen Komponenten beisammenhabt, startet ihr am besten mit einem Trockenaufbau außerhalb eurer Maschine. So könnt ihr das System zum Laufen bringen und kommt jederzeit problemlos an alle Stecker etc. heran.

Die Heizung eurer Maschine könnt ihr z. B. mit einer Glühbirne simulieren, jeder andere 230V Verbraucher tut es aber genauso gut.

Trockenaufbau
*(1=Mikrocontroller, 2=Temperatursensor, 3=SSR Relais für Heizung, 4=Schaltnetzteil, 5=Display)*

Das PCB für den Mikrocontroller sieht wie folgt aus:

PCB

###  Grundversion PID Only

Die einzelnen Komponenten werden wie folgt angeschlossen:

PIN | Belegung
-|-
PIN 14 | SSR Heizung     
PIN 2 | Temperatursensor
PIN 4 | Display-PIN SDA
PIN 5 | Display-PIN SCL
GND/Vin | Netzteil

### Vollausbau

Bei dem „Vollausbau“ wird noch die Steuerung für Magnetventil und Pumpe benötigt:

PIN | Belegung
-|-
PIN 12 | Relais Ansteuerung Magnetventil
PIN 13 | Relais Ansteuerung Pumpe

## Einbau

### Temperatursensor anschließen

Besondere Sorgfalt müsst ihr bitte beim Anschließen des Temperatursensors TSIC306 walten lassen: sobald dieser einmal falsch angeschlossen Spannung bekommen hat, ist er entweder sofort zerstört oder zumindest vorgeschädigt und liefert dadurch fehlerhafte Messwerte. Daher ist es immer ratsam einen Ersatz-Sensor parat zu haben.

* Sensor V+ : Board PIN 2 5V
* Sensor Signal: Board PIN 2 Signal
* Sensor GND:  Board PIN 2 GND

Wie ihr zu der Beschreibung zum Board sehen könnt, muss an Pin 2 der Temperatursensor angeschlossen werden. Die oberen Ports (14, 2, 12, 13, 15) sind einheitlich jeweils von links nach rechts mit Minus(-), Signal, 5V(+) belegt.

TSIC Sensor

Da wir öfters hören, dass die Bildbeschreibung zum TSIC nicht gut ist, haben wir hier nochmals die Pins vom Sensor dargestellt. Die flache Seite liegt unten. Ein falsch gepolter TSIC sollte entsorgt werden! Er misst vermeintlich richtig, aber definitiv nicht mehr genau.

Beim Anschließen des SSR zur Ansteuerung der Heizung ist es wichtig, dass die Polarität der SSR-Ports 3 und 4 beachtet werden:

* SSR Port 3 (+) : Board PIN 14 Signal
* SSR Port 4 (-) : Board PIN 14 GND

Damit habt ihr das System zum ersten Mal aufgebaut.

### PIN Belegung vom PCB

Pin|Funktion
-|-
Pin 12| Relay für das Ventil
Pin 13| Relay für die Pumpe
Pin 15| frei
Pin 14| Relay für die Heizung
Pin 2| Temperatursensor
A0| Schalter Brühtaste
|
Pin 4| SDA
Pin 5| SCL
Pin 16| frei



## Tipps und Tricks

Hier einige gesammelte Hinweise zum Einbau in die Maschine:

* Verbaut die Komponenten an einem trockenen Ort und möglichst entfernt von der Hitzequelle Boiler.

* Das SSR schaltet die Heizleistung von ca. 1.000 W, von daher kann eine Montage mit wärmeleitendem Kleber bzw. Klebepads nicht schaden.

*  Den Temperatursensor solltet ihr wenn möglich nicht nur an den Kessel ankleben, sondern fest verschrauben. Bei der Rancilio Silvia kann man dazu die Halteklammer des nun überflüssigen Brühthermostaten nutzen, bei der Gaggia Classic kann der Sensor am vorhandenen M4-Gewinde der Thermostataufnahme verschraubt werden.

* Zum Anschluss des Temperatursensors TSIC keine Steckverbinder (Jumperkabel) nehmen, sondern Litze an die Beine des TSIC löten. Das ist etwas fummelig, aber dafür habt ihr weniger Neigung zu Wackelkontakten im verbauten Zustand.

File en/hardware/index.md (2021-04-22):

---
layout: default
title: Hardware
parent: EN - Manual
has_children: true
nav_order: 5
---

# Hardware

This part contains the hardware related aspects of the PID, including the test assebly and installation.

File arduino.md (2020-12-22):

---
title: Arduino IDE einrichten
has_children: false
nav_order: 1
---

# Arduino IDE einrichten
{: .no_toc }

Inhaltsverzeichnis

* TOC
{:toc}

## Installationsvideo

In diesem kurzen Video erklären wir die Installation der Arduino IDE und zeigen wie unsere OpenSource Software Rancilio-PID auf dem NodeMCU installiert wird. Viel Spaß!

Installationsvideo (https://www.youtube.com/watch?v=w7vBGSVWPrw)

## Download

Wird benötigt, um den Code auf den Controller zu spielen.

[Link zu Arduino](https://www.arduino.cc/en/Main/Software)

Screenshot der Arduino Homepage

## Der Programmcode

Download des aktuellen Programmcode findest du im aktuellen Release.

[Link zum Github Repository](https://github.com/rancilio-pid/ranciliopid/releases)

Screenshot der Github Homepage

## Installation der Arduino IDE

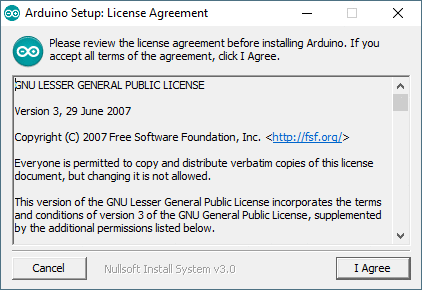
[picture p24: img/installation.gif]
Arduino Installation


Hinweise zur Installation befinden sich auf der [Arduino Homepage](https://www.arduino.cc/en/Guide).

Nach der erfolgreichen Installation kann Arduino über das Startmenü gestartet werden.

## Arduino Voreinstellungen

### Boardverwaltungs-URL anlegen

Wir benötigen für den Einsatz des NodeMCUs eine zusätzliche Boardverwaltungs-URL.

Diese erreicht ihr unter: Datei > Voreinstellungen

| Key | Value |
|-|-|
| Boardverwaltungs-URL | `http://arduino.esp8266.com/stable/package_esp8266com_index.json`|

<details markdown="block">
  <summary> Windows </summary>

  Windows Arduino Voreinstellungen

</details>

<details markdown="block">
  <summary> Linux (Ubuntu) </summary>

  Linux (Ubuntu)

</details>

### Boardtreiber installieren

Als nächstes müssen die ESP8266 Boardtreiber installiert werden.

Dies erreicht ihr unter: Werkzeuge > Board: "[\<Version\>]" > Boardverwalter...

<details markdown="block">
  <summary> Windows </summary>

  Windows Arduino Boardverwalter

</details>

<details markdown="block">
  <summary> Linux (Ubuntu) </summary>

  Linux (Ubuntu) Boardverwalter

</details>

Bitte die aktuelle Version installieren.

Typ \<Alle\> > "esp": "**esp8266** by **ESP8266 Community**"

ESP8266 installieren

Nun ist die Arduino IDE vorbereitet. Weiter geht es mit den Bibliotheken.

## Bibliotheken installieren

Der sicherste und einfachste Weg alle Bibliotheken korrekt zu installieren, ist es, die [Bibliotheken aus Github](https://github.com/rancilio-pid/ranciliopid/tree/master/rancilio-pid/libraries) zu nehmen. Diese solltet ihr bereits heruntergeladen haben (siehe [Programmcode](#der-programmcode)). Kopiert die kompletten Ordner einfach in den Arduino Libraries Ordner zu kopieren:

| OS | Arduino Libraries Ordner |
|-|-|
| Windows | `My Documents\Arduino\libraries\` |
| OSX | `~/Documents/Arduino/libraries/` |
| Linux |`~/Arduino/libraries`|

Wie immer ist es empfehlenswert beim offiziellen Guide mehr Infos einzuholen: [Link](https://www.arduino.cc/en/Guide/Libraries).

### Bibliotheken manuell installieren

Alternativ müssen folgende Libraries per Hand installiert werden:

* Blynk
* TimeLib
* WidgetRTC
* U8x8lib
* OneWire
* DallasTemperature
* PID_v1.h

Die Installation der einzelnen Bibliotheken erfolgt wieder über die Verwaltung in Arduino IDE:

Bibliotheken verwalten

<details markdown="block">
  <summary> OneWire </summary>

  
</details>

<details markdown="block">
  <summary>
    DallasTemperature
  </summary>


</details>

<details markdown="block">
  <summary> U8x8lib </summary>

  1. Geht auf [https://github.com/olikraus/u8g2](https://github.com/olikraus/u8g2)
  1. Code > Download Zip
  
  1. Legt die Dateien im [Arduino Libraries Ordner](#bibliotheken-installieren) ab
  1. Erstellen einen Ordner: `U8x8lib`
  1. Den Inhalt aus dem ZIP File Ordner: u8g2-master.zip\u8g2-master\cppsrc  UND csrc in den neu erstellten Ordner kopieren (ja, es sind eine ganze Menge Dateien :))
  
    
</details>

<details markdown="block">
  <summary> PID_v1.h </summary>

  1. Geht auf [https://github.com/br3ttb/Arduino-PID-Library](https://github.com/br3ttb/Arduino-PID-Library)
  1. Code > Download Zip  
  
  1. Legt die Dateien im [Arduino Libraries Ordner](#bibliotheken-installieren) ab
  1. Erstellen einen Ordner: `PID_v1`
  1. Die vier Dateien aus dem ZIP File kopieren und in den neuen Ordner einfügen:
  
    
</details>

<details markdown="block">
  <summary> Blynk </summary>

  1. Geht auf [https://www.blynk.cc/getting-started/](https://www.blynk.cc/getting-started/)
  
  1. Geht auf [https://github.com/blynkkk/blynk-library/releases/tag/v0.5.4](https://github.com/blynkkk/blynk-library/releases/tag/v0.5.4)
  
  
  
  
  1. Wechseln in den [Arduino Libraries Ordner](#bibliotheken-installieren)
  
    
</details>

## Board einstellen




Wenn alle Bibliotheken installiert sind, müsste es wie folgt aussehen:



Somit ist alles nun für das Einrichten von Blynk und das Flashen von dem Code vorbereitet. Dann kann der erste Test beginnen.

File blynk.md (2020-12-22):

---
title: Einrichtung von Blynk
parent: Der erste Test
has_children: false
nav_order: 1
---

# Einrichtung von Blynk
{: .no_toc }

Inhaltsverzeichnis

* TOC
{:toc}

## Einleitung

Als nächstes richtet ihr zur Bedienung des PIDs auf eurem Smartphone die App Blynk ein. Blynk ist ein Cloud“-Dienst, über den der NodeMCU mit dem Handy oder Tablet steuerbar ist. Freundlicherweise steht uns ein eigener Blynk Server zur Verfügung, den Markus hostet. Natürlich könntet Ihr auch den Public Server von Blynk nutzen, hättet ggf. aber Kosten für das Einrichten der App.

Vom Prinzip funktioniert es wie folgt:

Die Maschine sendet Daten an einen Blynk-Server. Die App greift ebenfalls auf den Server zu und holt sich die benötigten Daten ab. Das Ganze funktioniert bidirektional: der Blynk-Server stellt einerseits die Parameter zum Betrieb des PIDs bereit, andererseits empfängt er auch vom PID die Daten zum aktuellen Betriebszustand der Maschine. Ein Auth Token stellt hierbei sicher, dass nur euere Maschine gesteuert wird.

Auch hierzu hat Markus ein Video auf Youtube, in dem die Installation gut erläutert wird.

## Video: Installieren und einrichten der Blynk App

Installationsvideo (https://www.youtube.com/watch?v=JHDRUN044gQ)

## Schritt 1: App herunterladen

Siehe unter [https://www.blynk.cc/](https://www.blynk.cc/) gibt es für alle gängigen Betriebssysteme

## Schritt 2: Account anlegen

Öffnet hierzu die Blynk-App & Klickt auf „Create New Account“



Klickt jetzt zuerst auf das Ampel-Symbol um den Server zu wechseln!
Sonst nutzt Ihr den „normalen Blynk“-Server.



**WICHTIG**:

Legt den Schalter auf „Custom“ um.
Als Server tragt Ihr: blynk.remoteapp.de
Port: 9443
Bestätigt die Eingabe mit „OK“



Ergänzt jetzt eure E-Mail-Adresse:
Und klickt im Fenster auf „Next“



Der Account ist nun angelegt.
Erstellt euer erstes Projekt mit dem Klick auf „New Project“

Hier könnt ihr auch direkt auf das Scan-Symbol oben rechts klicken und folgenden Code einscannen:

QR-Code für Android:



QR-Code für IOS:



(Dargestellte PID Werte entsprechen nicht mehr den neusten Stand)



oder die App selbst erstellen.



Gebt dem Projekt einen sinnvollen Namen.
Als Device wählt bitte "NodeMCU".



AuthKey auslesen (wird im Arduino benötigt).
Klickt hierzu auf das Viereck oben Rechts.



Klick jetzt auf das „Muttern“-Symbol



Im unteren Bereich – steht der Auth-Code.
Dieser kann auch via E-Mail angefragt werden.
Der Auth-Code ist sozusagen der Schlüssel, zwischen NodeMCU und deinem Handy/Server.
Dieser Code sollte „Geheim“ bleiben.



## Schritt 3: Auth Token hinterlegen

Authkey wird im 2. Schritt in der userConfig.h hinterlegt. Bei Auth kommt der Code aus Blynk hinein. Bei SSID und PASS euer Wlan Name und Passwort. Dazu gleich mehr.



## Schritt 4: Aufbau der App

Klickt oben Rechts wieder auf das Viereck um in den Bearbeitungsmodus zu gelangen. Ihr müsst leider alle virtuelle PINS manuell in der App hinterlegen.





Pin | Wert
-|-
V2 | Input (aktuelle Temp)
V3 | Soll-Temp
V4 | P-Wert (Übergabe von Blynk an NodeMCU)
V5 | I-Wert (Übergabe von Blynk an NodeMCU)
V6 | D-Wert (Übergabe von Blynk an NodeMCU)
V7 | Einstellbare Soll-Temp
V8 | Preinfussion Brewtime
V9 | Preinfussion Start
V10 | Preinfussion Pause
V11 | P-Wert für den Startvorgang
V12 | Zielwert für den Startvorgang in °C
V13 | On/Off Schaltet die PID aus (Heizung auch)
V14 | Start I für Startvorgang
|
V20 | PID P Wert von interne PID an Blynk
V21 | PID I Wert von interne PID an Blynk
V22 | PID D Wert von interne PID an Blynk
V23 | Output Wert der internen PID
|
V30 | Brüherkennung: P Wert
V31 | Brüherkennung: I Wert
V32 | Brüherkennung: D Wert
V33 | Zeit in der die Brüherkennungs PID Werte aktiv sind
V34 | Wert bei dem die Brüherkennung aktiviert wird
V35 | Brüherkennungs Durchschnittswert
V36 | Brüherkennungs minimalWert

Die App ist in Widgets aufgebaut – die Widgets können via Drag-and-Drop einfach von rechts aus der Widget-Box in die App gezogen werden.



Einem Widget kann jetzt der INPUT Pin mitgeteilt werden (Siehe Liste oben)



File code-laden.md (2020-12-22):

---
title: Code Laden
parent: Der erste Test
has_children: false
nav_order: 2
---

# Code Laden
{: .no_toc }

Inhaltsverzeichnis

* TOC
{:toc}

## Code auf den Controller laden

Im aktuellen Release befinden sich zwei Datein:
* rancilio-pid.ino
* userConfig.h

Die rancilio-pid.ino ist das eigentliche Programmcode und die userConfig.h eine ausgelagerte Konfigurationsdatei. Diese einhaltet folgende Punkte.

### Vorab Konfig

Die wichtigsten Funktionen müssen hier parametriert werden. Denkt daran, den richtigen PID Mode, Temperatursensor und das ggf. passende Display auszuwählen.

```
define DISPLAY 2 // 1=U8x8libm, 0=Deaktiviert, 2=Externes 128x64 Display

define OFFLINEMODUS 0 // 0=Blynk und WLAN wird benötigt 1=OfflineModus (ACHTUNG EINSTELLUNGEN NUR DIREKT IM CODE MÖGLICH)

define ONLYPID 0 // 1=Nur PID ohne Preinfussion, 0=PID + Preinfussion

define TEMPSENSOR 2 // 1=DS19B20; 2=TSIC306

define BREWDETECTION 1 // 0 = off ,1 = Software, 2 = Hardware

define FALLBACK 1 // 1: fallback auf eeprom Werte, wenn blynk nicht geht 0: deaktiviert

define TRIGGERTYPE HIGH // LOW = low trigger, HIGH = high trigger relay

define OTA true // true=activate update via OTA

define PONE 1 // 1 = P_ON_E (normal), 0 = P_ON_M (spezieller PID Modus, ACHTUNG andere Formel zur Berechnung)
```

### Wifi

Unter Wifi müsst ihr euren Auth Token aus Blynk eintragen und eure Wlan SSID und das zugehörige Passwort. Bei der WLAN SSID bitte drauf achten, dass keine Leerzeichen darin enthalten sind! Auch Sonderzeichen machen gerne Schwierigkeiten im Betrieb.

```
#define AUTH "blynkauthcode"

#define D_SSID "wlanname"

#define PASS "wlanpass"
```

### OTA

Hier wird der Update **O**ver **T**he **A**ir eingestellt.

### PID

Hier definiert ihr eure initialen PID Werte.

## Temperatursensor anschließen

Wie ihr zu der Beschreibung zum Board sehen könnt, muss an Pin 2 der Temperatursensor angeschlossen werden. Die oberen Ports (14, 2, 12, 13, 15) sind einheitlich jeweils von links nach rechts mit Minus(-), Signal, 5V(+) belegt.



Da wir öfters hören, dass die Bildbeschreibung zum TISIC nicht gut ist, haben wir hier nochmals die Pins vom Sensor dargestellt. Die flache Seite liegt unten. Ein falsch gepolter TISIC sollte entsorgt werden! Er misst vermeintlich richtig, aber definitiv nicht mehr genau.

## PIN Belegung vom PCB

Pin|Funktion
-|-
Pin 12| Relay für das Ventil
Pin 13| Relay für die Pumpe
Pin 15| frei
Pin 14| Relay für die Heizung
Pin 2| Temperatursensor
A0| Schalter Brühtaste
|
Pin 4| SDA
Pin 5| SCL
Pin 16| frei



## Code hochladen und testen

Wenn ihr die .ino Datei öffnet, öffnet sich automatisch im zweiten Tab die userConfig.h mit den wichtigen Einstellungen. Danach auf den Pfeil klicken Achtet drauf, dass Ihr schon einen Auth-Code der Blynk-App und die WLAN-Zugangsdaten im Code der userConfig.h hinterlegt habt.



Bitte achtet vorher drauf, dass Ihr in den Board Einstellungen den richtigen COM Port ausgewählt habt.

Diesen könnt ihr auch auch im Gerätemanager prüfen (falls ihr ihn nicht wisst)





Den erfolgreichen Test könnt ihr einmal am Handy die Raumtemperatur sehen, wenn ihr korrekt den Temperatursensor angeschlossen habt, und auf dem Serial Monitor erkennen, wie sich der NodeMCU mit Blynk verbindet.



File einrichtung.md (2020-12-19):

# Arduino IDE einrichten

Inhaltsverzeichnis

## Download

Wird benötigt, um den Code auf den Controller zu spielen.

https://www.arduino.cc/en/Main/Software

Screenshot der Ardiuno Homepage

## Der Programmcode

Download des aktuellen Programmcode findest du im aktuellen Release.

https://github.com/rancilio-pid/ranciliopid/releases

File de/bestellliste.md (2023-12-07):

---
layout: default
title: Bestellliste
parent: DE - Handbuch
has_children: false
nav_order: 2
---

# Bestellliste
{: .no_toc }

Inhaltsverzeichnis

* TOC
{:toc}

## Warnhinweis

> {{ site.warnhinweis }}

## Die Liste

Du benötigst folgende Dinge:
(Einige davon sind sicher auch schon zu Hause in der Bastelkiste vorhanden)

### Basics

Die Basics werden auf jeden Fall benötigt und liegen (in der Regel) nicht irgendwo in der Werkstatt rum. In Klammern steht die Mindestanzahl.
Der zu verwendende Controller (ESP8266 oder ESP32) richtet sich nach der von euch bestellen Platine.

Beschreibung | ID | Anzahl PID Only | Anzahl Vollausbau | Link
-|-|-|-|-
Temperatur Sensor|TSIC 306 TO92|2 (1)|2 (1)|[Reichelt-Link](https://www.reichelt.de/tsic-digitale-halbleiter-temperatursensoren-tsic-306-to92-p82327.html?r=1), [Alternativer Shop](https://shop.bb-sensors.com/Messtechnik-je-Branche/Gebaeudetechnik/Digitaler-TSic-306-Temperatursensor-TO92.html), [Alternativer Sensor](https://www.reichelt.de/de/de/tsic-digitale-halbleiter-temperatursensoren-tsic-206-to92-p82326.html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)
Schaltnetzteil|APV-8-5|1|1|[Reichelt-Link](https://www.reichelt.de/led-trafo-7-w-5-v-dc-1400-ma-mw-apv-8-5-p170873.html?&trstct=pos_0&nbc=1) oder [Amazon-Link](https://www.amazon.de/gp/product/B06Y29GSHH/)
SSR Relais – Heizung|RA 2425-D06|1|1|[Reichelt-Link](https://www.reichelt.de/solid-state-relais-ust-2-32vdc-ulast-24-280v-ra-2425-d06-p22691.html?&trstct=pos_0)
Mikrocontroller|NodeMCU V2 ESP8266 ODER ESP32 (je nach Platine)|1|1|ESP8266: [Amazon-Link](https://www.amazon.de/AZDelivery-NodeMCU-ESP8266-ESP-12E-Development/dp/B06Y1LZLLY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) oder [Ebay-Link](https://www.ebay.de/itm/NodeMCU-v3-2-ESP8266-Dev-Kit-WIFI-Lolin-Amica-CP2102-v2-Arduino-IOT/252712258856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) oder [unverlötet (Amazon)](https://www.amazon.de/-/en/AZDelivery-NodeMCU-Amica-Unsoldered-Parent/dp/B07GYW4T5F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) ODER ESP 32 V4:[ESP32 Dev Kit C V4](https://www.amazon.de/-/en/AZDelivery-Development-Compatible-Including-Successor/dp/B07Z83MF5W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)
Display (optional aber empfehlenswert)|128 x 64 Pixel OLED SSD1306 |1|1|[Amazon-Link](https://www.amazon.de/AZDelivery-Display-Arduino-Raspberry-gratis/dp/B01L9GC470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)
unsere erstellte Platine|PCB|1|1|siehe unten

### Kabel

#### Hitzebeständige Kabel

Im folgenden die empfohlenen, hitzebeständigen Kabel.

Beschreibung | ID | Anzahl PID Only | Anzahl Vollausbau | Link
-|-|-|-|-
Hochtemperaturader ÖLFLEX® HEAT 180 SIF 1 x 1.50 mm², schwarz|601382|2|2|[Link](https://www.conrad.de/de/p/lapp-0051001-hochtemperaturader-oelflex-heat-180-sif-1-x-1-50-mm-schwarz-meterware-601382.html)
Hochtemperaturader ÖLFLEX® HEAT 180 SIF 1 x 1.50 mm², blau|600368|2|2|[Link](https://www.conrad.de/de/p/lapp-0051002-hochtemperaturader-oelflex-heat-180-sif-1-x-1-50-mm-blau-meterware-600368.html)
Hochtemperaturader ÖLFLEX® HEAT 180 SIF 1 x 0.25 mm², schwarz|604025|2|2|[Link](https://www.conrad.de/de/p/lapp-0047001-hochtemperaturader-oelflex-heat-180-sif-1-x-0-25-mm-schwarz-meterware-604025.html)
Hochtemperaturader ÖLFLEX® HEAT 180 SIF 1 x 0.25 mm², rot|603963|2|2|[Link](https://www.conrad.de/de/p/lapp-0047104-hochtemperaturader-oelflex-heat-180-sif-1-x-0-25-mm-rot-meterware-603963.html)
Hochtemperaturader ÖLFLEX® HEAT 180 SIF 1 x 0.25 mm², grün|609459|2|2|[Link](https://www.conrad.de/de/p/lapp-0047006-hochtemperaturader-oelflex-heat-180-sif-1-x-0-25-mm-gruen-meterware-609459.html)
Hochtemperaturader ÖLFLEX® HEAT 180 SIF 1 x 0.25 mm², gelb|602330|2|2|[Link](https://www.conrad.de/de/p/lapp-0047005-hochtemperaturader-oelflex-heat-180-sif-1-x-0-25-mm-gelb-meterware-602330.html)

#### Normale Kabel

Im folgenden die normalen Kabel. Diese werden nicht empfohlen, sind aber bei entsprechender Führung auch einsetzbar.

Beschreibung | ID | Anzahl PID Only | Anzahl Vollausbau | Link
-|-|-|-|-
Schaltlitze H07V-K, 1,5 mm, 10 m, blau|H07VK 1,5-10BL|1|1|[Link](https://www.reichelt.de/schaltlitze-h07v-k-1-5-mm-10-m-blau-h07vk-1-5-10bl-p69504.html?)
Schaltlitze H07V-K, 1,5 mm, 10 m, schwarz|H07VK 1,5-10SW|1|1|[Link](https://www.reichelt.de/schaltlitze-h07v-k-1-5-mm-10-m-schwarz-h07vk-1-5-10sw-p69503.html?)
Kupferlitze isoliert, 10M, 1×0,14mm², schwarz|LITZE SW|1|1|[Link](https://www.reichelt.de/kupferlitze-isoliert-10-m-1-x-0-14-mm-schwarz-litze-sw-p10298.html?)
Kupferlitze isoliert, 10M, 1×0,14mm², blau|LITZE BL|1|1|[Link](https://www.reichelt.de/kupferlitze-isoliert-10-m-1-x-0-14-mm-blau-litze-bl-p10292.html?)
Kupferlitze isoliert, 10M, 1×0,14mm², rot|LITZE RT|1|1|[Link](https://www.reichelt.de/kupferlitze-isoliert-10-m-1-x-0-14-mm-rot-litze-rt-p10297.html?)
Kupferlitze isoliert, 10M, 1×0,14mm², grün|LITZE GN|1|1|[Link](https://www.reichelt.de/kupferlitze-isoliert-10-m-1-x-0-14-mm-gruen-litze-gn-p10296.html?)

### Zubehör

Das Zubehör wird auf jeden Fall empfohlen. In einer gut sortierten Werkstatt findet man ggf. das ein oder andere bereits.

Beschreibung | ID | Anzahl PID Only | Anzahl Vollausbau | Link
-|-|-|-|-
Flachsteckhülsen mit Schrumpfschlauch – 1,5 … 2,5 mm², blau|WE F602638HS|10|20|[Reichelt-Link](https://www.reichelt.de/flachsteckhuelsen-mit-schrumpfschlauch-1-5-2-5-mm-blau-we-f602638hs-p189402.html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)
Flachsteckhülsen mit Abzweig – 1,5 … 2,5 mm², transp., vollisoli|WE F606638.1N|5|5|[Reichelt-Link](https://www.reichelt.de/flachsteckhuelsen-mit-abzweig-1-5-2-5-mm-transp-vollisoli-we-f606638-1n-p189372.html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)
Flachstecker mit Schrumpfschlauch – 1,5 … 2,5 mm², blau|WE F616638HS|10|20|[Reichelt-Link](https://www.reichelt.de/flachstecker-mit-schrumpfschlauch-1-5-2-5-mm-blau-we-f616638hs-p189408.html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)
Ring-Kerbschuhe, für M3, rot|RK-R-3|10|10|[Reichelt-Link](https://www.reichelt.de/ring-kerbschuhe-fuer-m3-rot-rk-r-3-p15259.html?&nbc=1)
Ring-Kerbschuhe, für M5, rot|RK-R-5|10|10|[Reichelt-Link](https://www.reichelt.de/ring-kerbschuhe-fuer-m5-rot-rk-r-5-p142770.html?&nbc=1)
Relais für **Vollausbau** (siehe unten)|DEBO RELAY 4WAY|0|1|[Reichelt-Link](https://www.reichelt.de/entwicklerboards-4-wege-solid-relais-5v-240v-2a-debo-relay-4way-p280064.html?)
Schrumpfschlauch|DELOCK 86271|1|1|[Link](https://www.reichelt.de/schrumpfschlauch-sortiment-schwarz-100-teilig-delock-86271-p152924.html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)
Schraube M4x16||1|1|
Mutter M4||2|2|
Unterlegscheibe M4||2|2|
Wärmeleitkleber (nichtleitend) für den Sensor|Silverbead Wärmeleitkleber|||[Link](https://www.amazon.de/Silverbead-W%C3%A4rmeleitkleber-10-Gramm-SG100X/dp/B019MNSABG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)
alternativ||||
Wärmeleitpaste für den Sensor|ARCTIC MX-4-2|||[Link](https://www.reichelt.de/arctic-mx-4-waermeleitpaste-2g-arctic-mx-4-2-p261247.html?&trstct=pos_14&nbc=1)
Jumperkabel (optional)| AZDelivery Jumper Wire Kabel 3 x 40 STK | 1 | 1 | [Amazon-Link](https://www.amazon.de/Jumper-Wire-Set-M2M-Parent/dp/B07ZP4JLMM)
alternativ | siehe unten
Dupont-Stecker (optional) | Dupont Stecker | 1 | 1 | [Reichelt-Link](https://www.reichelt.de/de/de/entwicklerboards-dupont-crimp-set-610-teilig-debo-set-dupont-p279901.html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) oder [Amazon-Link](https://www.amazon.de/BESTOMZ-Stecker-m%C3%A4nnlich-weiblich-Anschluss/dp/B073SSV9TL/)
Crimpzange|KN 97 22 240|||[Link](https://www.reichelt.de/crimpzange-240-mm-isolierte-kabelschuhe-kabelverbinder-kn-97-22-240-p122639.html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)
Lötkolben|ERSATZKOLBEN EP5|||[Reichelt-Link](https://www.reichelt.de/loetkolben-ep-5-ersatzkolben-ep5-p58217.html?&trstct=pos_0&nbc=1)

## Anmerkungen zur Bestelliste

### ESP32 Platine
Es steht ab sofort die neue ESP32 Platine zur Verfügung. 
[Bitte direkt über unseren Chat anfragen!](https://discord.com/invite/Kq5RFznuU4) **Bitte direkt per PN an @loque wenden**
**Stand 7.12.23: Momentan sind keine ESP32 Platinen verfügbar. Vorraussichtlich ab Januar wieder bestellbar**

Inklusive sind:
 * Das PCB
 * Die Schraubklemmenblöcke
 * Die Stiftleisten
 * Klebepads

**ZUSÄTZLICH** werden folgende Dinge benötigt:

Bauteil | Beschreibung | Link
-|-|-
C1 |220µF (Elko) | [Link](https://www.reichelt.de/elko-radial-220-uf-10-v-105-c-low-esr-fm-a-220u-10-p200036.html?&trstct=pol_0&nbc=1)
C2 |100nF (Keramik) | [Link](https://www.reichelt.de/vielschicht-kerko-100-nf-50-v-rm-5-125-c-hita-sf1h104z-l5-p246835.html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)
R1 |4,7kΩ (Display) | [Link](https://www.reichelt.de/widerstand-metallschicht-4-7-kohm-0204-0-4-w-1--yag-4fte52-4k7-p236963.html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)
R2 |4,7kΩ (Display) |[Link](https://www.reichelt.de/widerstand-metallschicht-4-7-kohm-0204-0-4-w-1--yag-4fte52-4k7-p236963.html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)
R3 |47kΩ (Brew switch) | [Link](https://www.reichelt.de/widerstand-metallschicht-47-kohm-axial-0-4-w-1--vis-c4702fc100-p237115.html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)
R4 |47kΩ (Power switch) |[Link](https://www.reichelt.de/widerstand-metallschicht-47-kohm-axial-0-4-w-1--vis-c4702fc100-p237115.html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)
R5 |47kΩ (Steam switch) |[Link](https://www.reichelt.de/widerstand-metallschicht-47-kohm-axial-0-4-w-1--vis-c4702fc100-p237115.html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)
R6 | Nach Bedarf | Widerstand entsprechend der gewählten LED nehmen, bei Nutzung von z.B. Neopixel braucht es keinen Widerstand, dafür Lötjumper JP1 schließen 

Beim Löten des Elkos auf die Polarität achten!

**Bugs ESP32_mininmal PCB Rev 1.2:**

Fehler in der Beschriftung:

* S_LED: statt VCC muss hier 5V stehen
* E_TRIG: statt VCC muss hier 5V stehen
* W_SENS: statt IO36 muss hier IO23 stehen
* GPIO Header:  statt IO23 muss hier IO36 stehen 

Fehler Optokoppler für Brüherkennung:

* Nur mit High Level Trigger Optokoppler kompatibel
* Workaround für Low Level Trigger: Pulldown Widerstand R3 nicht einlöten und "PINMODEVOLTAGESENSOR" auf "INPUT_PULLUP" setzen 

**Bugs EPS32_minimal PCB Rev 1.3:**

Fehler Optokoppler für Brüherkennung:

* Nur mit High Level Trigger Optokoppler kompatibel
* Workaround für Low Level Trigger: Pulldown Widerstand R3 nicht einlöten und "PINMODEVOLTAGESENSOR" auf "INPUT_PULLUP" setzen 

### ESP8266 Platine

[Bitte direkt über unseren Chat anfragen!](https://discord.com/invite/Kq5RFznuU4) **Bitte direkt per PN an @loque wenden**

PCB Lieferumfang

Inklusive sind:
 * Das PCB
 * Die Schraubklemmenblöcke
 * Die Stiftleisten
 * Klebepads

### Infos zum Wärmeleitkleber
Wärmeleitkleber/-paste ist umstritten (siehe [Link](https://www.igorslab.de/mythos-waermeleitpaste-edelpaste-zum-apothekenpreis-gegen-guenstiges-massenprodukt-wir-rechnen-gnadenlos-nach/) und Block unten zur Herleitung). Nichtsdestotrotz befestigen einige Anwender den TSIC mit dem Kleber direkt am Kessel. Zusammenfassend kann man sagen: Tragt möglichst wenig davon auf. Alternativ zum Kleben befestigt ihr den Sensor besser mit der nun leeren Halterung des Thermostats (und einer zusätzlichen Schraube und Mutter). Damit sollte sich ein akzeptables Maß aus Temperaturdifferenz und sicherer Befestigung erreichen lassen.

<details markdown="block">
  <summary> Diskussion zum Wärmeleitkleber </summary>

  Wie oben bereits erwähnt ist Wärmeleitkleber wegen seiner schwachen Wärmeleitfähigkeit umstritten. Einer der wenigen _empfehlenswerten_ Wärmeleitkleber ist von Arctic Silver mit einer Wärmeleitfähigkeit von 4 W/mK im vernetzten Zustand: [Link](https://www.webshop-innovatek.de/waermeleitmittel/waermeleitkleber/368/arctic-silver-waermeleitkleber-2x-4-g-neue-version) (leider nur schwer bzw. zu Apothekenpreisen erhältlich). Der oben verlinkte Kleber verfügt hingegen nur über eine Wärmeleitfähigkeit von etwa 1 W/mK (unter der Annahme, dass die Angaben korrekt sind).

  Als Bsp. für die Paste würde eine Schichtdicke von 0,05 mm einen Wärmeleitwiderstand von 0,29 K/W ergeben. Bei 0,5 mm sind wir schon bei 2,9 K/W.

  Das bedeutet das bei einer Verlustleistung von 1 W die Temperaturdifferenz zwischen Quelle (Boiler) und Senke (Sensor) bei 0,29 bzw. 2,9 K liegt.

  Aus diesem Grund ist es sehr wichtig, das die Paste oder zur Not der Kleber so **DÜNN WIE MÖGLICH** aufgetragen wird! Wir reden hier im Optimalfall von 0,04 mm.

</details>

### Infos zum Temperatursensor
Wir geben hier den Tipp gleich mindestens 2 TSIC Sensoren zu kaufen. Wir haben es nun häufiger erleben müssen, dass die Sensoren falsch verdrahtet werden oder diese anderweitig beschädigt sind. Daher denkt einfach gleich an eine Reserve bei der Bestellung bei Reichelt. Bitte einen falsch verpolten Sensor nicht mehr verwenden, dieser geht kurzfristig kaputt oder zeigt unrealistische Werte an (für Details siehe [Temperatursensor anschließen](./hardware/hardware.md#temperatursensor-anschließen)).

### Infos zum Microcontroller
Man kann beim NodeMCU **nicht** die V1 oder V3 nehmen. Nur die V2 passt auf das PCB. In Kürze werden neuere Versionen der Software nur noch mit ESP32 kompatibel sein, hier muss es das DevKitC V4 sein (mit ESP32, nicht ESP32S oder C etc.)

### Infos zu den Steckern
Es sind jeweils mehr Stecker als benötigt angegeben. Es ist empfehlenswert hier eher mehr zu Bestellen, da gerne mal etwas schief läuft und man sonst ohne Kaffee auf die neue Bestellung warten muss.

### Infos zum Netzteil
Das Netzteil hat bei wenigen Personen zu Problemen geführt (Reboots).
Insbesondere bei den neueren Rancilio Silvia E Varianten oder kleineren Maschinen ist auch der Platz ein Thema. Eine Alternative kann in beiden Fällen ein einfaches USB Netzteil sein, für welches aber eine ordentliche Kontaktierung schwierig ist.

### Infos zum Display und Jumper (bzw. Dupont)
Das Display wird für keine Ausbaustufe zwangsläufig benötigt. Ohne Display lässt es sich jedoch kaum vermeiden, dass man bei jedem Bezug am Smartphone die Temperatur prüfen muss. Im regulären Lauf sieht die Anzeige nämlich wie folgt aus (es wird in kurzen Intervallen geheizt um die Temperatur zu halten):

Regulärer Lauf | Auszug Monitoring (Grafana)
:---:|:---:
Blinken|Blink Monitoring

Wer es einfach mag, kann das Display entweder neben die Maschine legen, oder an einem der Bleche fixieren. Wie ihr einzelnen Bauberichten entnehmen könnt ([Link](https://clevercoffee.de/rancilio-silvia-e-konstantin/)), kann das Display natürlich auch sauber hinter einem der Bleche integriert oder mit einem 3D-gedruckten Gehäuse an der Maschine befestigt werden.

Für einen ersten Betrieb des Displays empfehlen sich die gelisteten Jumperkabel - so muss nicht zwangsläufig gelötet werden. Jumper sind gut für den Trockenaufbau geeignet, haben aber keinen ausreichend stabilen Halt an den Pins für den dauerhaften Einbau.
Alternativ könnt ihr euch ein Dupont-Set mit Crimpzange zulegen. Dieses hat den Vorteil, dass ihr die Länge der Verbindung frei zuschneiden könnt. Es kann aber nur mit einer Crimpzange genutzt werden kann. Dupont-Stecker sind gut für den finalen Einbau geeignet und man muss ebenfalls nicht am Display löten.
Beachtet jedoch den entsprechenden Hinweis zum Temperatursensor (dieser sollte gelötet werden): [Link](./hardware/hardware.md/#tipps-und-tricks).

### Infos zum Vollausbau SSR
Wir haben im Projekt viele diverse Relais für die Pumpe und das Ventil testen „dürfen“ – diese sind leider nicht so stabil wie die der SSR für die Heizung. Folgende Erkenntnisse haben wir dabei gesammelt:

#### Beste Lösung: High Trigger SSR
User im Chat haben zuverlässige Bezugsquellen für High Trigger gefunden: [Link](https://www.roboter-bausatz.de/1450/2-kanal-solid-state-relais-modul-5v/230vac-high-level-trigger). Daher ist dies momentan unsere Favorit.

Alternativ kann bei Reichelt auch folgender High Trigger mitbestellt werden: [Link](https://www.reichelt.de/entwicklerboards-4-wege-solid-relais-5v-240v-2a-debo-relay-4way-p280064.html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).

Bei einigen SSR-Ralais, z.B. dem von Reichelt muss ggf. noch ein Widerstand parallel zu der Pumpe geschaltet werden. Hintergrund hierzu ist, dass die SSRs in der Regel nur bei einem Nulldurchgang der Spannungskennlinie schalten. Die Vibrationspumpe in den Espressomaschinen funktioniert jedoch durch eine interne Diode die nur eine Halbwelle durchlässt. Dementsprechend kommt es nie zu einem Nulldurchgang. Einige Relais funktionieren trotzdem. Um diesem Problem Abhilfe zu schaffen wird ein Widerstand parallel zu der Pumpe geschaltet. Aus Erfahrung funktionieren 200k und 100k Widerstände. Wobei ein 100k Widerstand an dieser Stelle sinnvoller ist. Zu beachten ist hier die Leistung die über dem Widerstand abfällt. Die normalen "Wald und Wiesen" Widerstände die in Sortimentskästen verkauft werden haben nur 1/4 Watt was bei 200k recht grenzwertig und bei 100k unzureichend ist. Auf der sicheren Seite ist man mit einem 100k Widerstand mit 1W. Wie z.B. [Link](https://www.reichelt.de/widerstand-metalloxyd-100-kohm-0207-1-0-w-5--1w-100k-p1778.html?&trstct=pos_1&nbc=1) 

#### Schlechteste Lösung: Spulen Relais
Ja, Spulen Relais kann man verwenden, dabei können durch die Bauweise der Relais Probleme entstehen, die sich nicht immer lösen oder reproduzieren lassen: [Link](https://www.amazon.de/AZDelivery-2-Relais-Optokoppler-Low-Level-Trigger-Arduino/dp/B078Q326KT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). Lösungen mit einer galvanischen Trennung können manchmal helfen [Link](https://www.kollino.de/arduino/4-8-kanal-relais-anleitung/). Daher ist es die schlechteste Lösung bei den Relais.

#### SSR-Board von Amazon
Manche gehen ins Spielcasino, wir bestellen bei Amazon – Manchmal hat man Pech und wo „High Trigger“ drauf steht, ist doch „Low Trigger“ drin. Einen Low Trigger erkennt ihr an einem „2TY“ auf dem einen Baustein des SSR-Boards. „J3Y“ ist hierbei der besser geeignete HIGH Trigger. SSR Boards sind besser als die Spulen-Relais, aber Low Trigger können auch Probleme verursachen.

#### Alternative: 2x Heizungs-SSR
Wenn der Platz vorhanden ist, könnte man auch 2x den Heizung SSR nutzen.

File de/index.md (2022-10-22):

---
layout: default
title: DE - Handbuch
has_children: true
nav_order: 1
---

## Handbuch (deutsch)

Dies ist das deutsche Handbuch für die Umsetzung des CleverCoffee Projektes. Dieses Handbuch deckt alle notwendigen Schritte für den Einbau und die Konfiguration ab.

Es ist sehr empfehlenswert zuerst die einleitenden Artikel zu lesen. Dadurch erfährt man, welche Anforderungen erfüllt sein müssen, um eine Maschine mit einem PID zu ergänzen. Außerdem wird beschrieben was das vorgestellte System kann (und was es nicht kann). 

Der erste konkrete Schritt beginnt mit der Bestellliste. Je nach Ausbaustufe und bereits vorhandener Ausstattung, setzt sich diese unterschiedlich zusammen. Während ihr auf die Hardware wartet, könnt ihr damit beginnen die Software aufzusetzen. Danach wird beides vereint und eingebaut. Nach erfolgreichem Test findet ihr im letzten Abschnitt noch eine Vielzahl von Anpassungsmöglichkeiten, damit auf keinen Fall lange Weile aufkommt.

Mehr zum Projekt findet ihr auf der [CleverCoffee Website](https://clevercoffee.de/).

## Kontakt
Schaut am besten beim [Chat-Server](https://chat.rancilio-pid.de/) vorbei.

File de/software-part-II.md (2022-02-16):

---
layout: default
title: Software Teil II
parent: DE - Handbuch
has_children: false
nav_order: 6
---

# Software Teil II
{: .no_toc }

Inhaltsverzeichnis

* TOC
{:toc}

## Einleitung

In diesem Kapitel wird beschrieben wie der Code auf den Mikrocontroller (NodeMCU) geladen wird. Damit könnt ihr loslegen, sobald ihr den Mikrocontroller zur Hand habt (weitere Teile werden nicht hierfür nicht benötigt). Für einen Test sollte dann zumindest der Temperatursensor angeschlossen werden.

## userConfig.h
In dem rancilio-pid/rancilio-pid Ordner befindet sich eine für euch wichtige Datei: 
* userConfig_sample.h

Die userConfig_sample.h muss in userConfig.h umbenannt werden und mit euren Werten anpasste werden. 
Alle wichtigen Einstellungen werden für eure PID in dieser Datei vorgenommen, diese werden nun gleich genauer erläutert.
Bei einem Update auf eine neuere Version bitte unbedingt die neuste userConfig_sample.h nehmen und mit euren Werten anpassen.
Wenn Ihr das nicht tut, kann dies zu unspezifischen, nicht erwünschten Verhalten an der Maschine kommen: Display hängt, PID geht nicht und weitere

## Die Parameter in der userConfig.h

Die userConfig.h ist in mehrere Abschnitte unterteilt. Die wir nun nach und nach euch vorstellen werden. 

### List of supported machines

Die Aufzählung MACHINE enthält alle bislang unterstützen Maschinen.
```
enum MACHINE {
  RancilioSilvia,   // MACHINEID 0
  RancilioSilviaE,  // MACHINEID 1
  Gaggia,           // MACHINEID 2
  QuickMill         // MACHINEID 3
};
```

### MACHINEID
```
#define MACHINEID 0                //  see above list of supported machines
```
Hier müsst ihr die ID eurer Maschine eintragen. Dieser Parameter steuert die Logodarstellung auf dem Display (wenn angeschlossen) und bei der Quick Mill die Erkennung des Brühvorgangs und den Dampfmodus bei BREWDETECTION 3.

### DISPLAY
Hier werden alle Display relevanten Einstellungen vorgenommen. 
```
#define DISPLAY 2                  // 0 = deactivated, 1 = SH1106 (e.g. 1.3 "128x64), 2 = SSD1306 (e.g. 0.96" 128x64)
#define OLED_I2C 0x3C		           // I2C address for OLED, 0x3C by default
#define DISPLAYTEMPLATE 3          // 1 = Standard Display Template, 2 = Minimal Template, 3 = only Temperatur, 4 = Scale Template, 20 = vertical Display see git Handbook for further information
#define DISPLAYROTATE U8G2_R0      // rotate display clockwise: U8G2_R0 = no rotation; U8G2_R1 = 90°; U8G2_R2 = 180°; U8G2_R3 = 270°
#define SHOTTIMER 1                // 0 = deactivated, 1 = activated 2 = with scale
#define HEATINGLOGO 0              // 0 = deactivated, 1 = Rancilio, 2 = Gaggia 
#define OFFLINEGLOGO 1             // 0 = deactivated, 1 = activated
#define BREWSWITCHDELAY 3000       // time in ms
#define LANGUAGE 1                 // LANGUAGE = 0 (DE), LANGUAGE = 1 (EN), LANGUAGE = 2 (ES)
```
DISPLAY definiert den Displaytyp. 

OLED_I2C gibt die I2C Adresse an, hier muss in der Regel nichts angepasst werden.  

DISPLAYTEMPLATE definiert das Template was ihr verwenden möchtet, siehe [Displayausgabe](https://manual.rancilio-pid.de/de/customization/Display.html).

DISPLAYROTATE lässt das Display rotieren. Beim Hochformat muss ein entsprechendes vertikale Displaytemplate (20) verwendet werden.

SHOTTIMER (1) lässt euch den Shottimer aktivieren, bei der Verwendung einer Waage kann (2) ausgewählt werden, um auch das Gewicht zu sehen.

HEATINGLOGO zeigt euch bis kurz vor Erreichen der Solltemperatur ein entsprechendes Logo anzeigen, siehe [Displayausgabe](https://manual.rancilio-pid.de/de/customization/Display.html).

OFFLINEGLOGO zeigt euch beim deaktivieren der PID via Blynk ein Logo an, siehe [Displayausgabe](https://manual.rancilio-pid.de/de/customization/Display.html).

BREWSWITCHDELAY ermöglicht euch einzustellen, wie lange die letzte Dauer beim Bezug im Display angezeigt werden soll.

LANGUAGE erlaubt es die Sprache für Displayausgaben auszuwählen.  

### Offline mode
Hier wird definiert, wie die PID sich im Offline Betrieb verhalten soll. 
```
#define OFFLINEMODUS 0             // 0 = Blynk and Wifi are used, 1 = offline mode (only preconfigured values in code are used!)
#define FALLBACK 1                 // 1 = fallback to values stored in eeprom, 0 = deactivated
#define GRAFANA 1                  // 1 = grafana visualisation (access required), 0 = off (default)
```
OFFLINEMODUS: Mit (0) wird eure PID mit Blynk und WlAN arbeiten. Bei (1) bleibt die PID offline. Daher werden alle vordefinierten PID Werte aus der userConfig.h genommen. 

FALLBACK gibt euch die Möglichkeit, dass die PID die letzten im EEPROM gespeicherten Werte nimmt, falls kein WLAN vorhanden ist. Das kann euch helfen, wenn die Maschine im Büro oder im Bereich ohne WLAN steht. Dann kann die Maschine auf den Hotspot des Handy eingestellt sein und bei Bedarf stellt man die Werte per Hotspot und Blynk ein und wenn kein WLAN vorhanden ist, nimmt die Maschine die letzten Werte. Diese werden bei jeder erfolgreichen Verbindung mit Blynk beim Start der Maschine gespeichert. 

GRAFANA aktiviert die Visualisierung mittels Grafana, diese muss in Blynk noch weiter definiert werden. 
## PID & Hardware
Hier sind die wichtigsten Parameter für die PID/Hardware definiert,
```
#define ONLYPID 1                  // 1 = Only PID, 0 = PID and preinfusion
#define ONLYPIDSCALE 0             // 0 = off , 1= OnlyPID with Scale
#define BREWMODE 1                 // 1 = NORMAL preinfusion ; 2 = Scale with weight
#define BREWDETECTION 1            // 0 = off, 1 = Software (Onlypid 1), 2 = Hardware (Onlypid 0), 3 = Sensor/Hardware for Only PID 
#define COLDSTART_PID 1            // 1 = default coldstart values, 2 = custom values via blynk (expert mode activated) 
#define TRIGGERTYPE HIGH           // LOW = low trigger, HIGH = high trigger relay
// BREWDETECTION 3 configuration
#define VOLTAGESENSORTYPE HIGH 
#define PINMODEVOLTAGESENSOR INPUT // Mode INPUT_PULLUP, INPUT or INPUT_PULLDOWN_16 (Only Pin 16)
```
ONLYPID definiert, ob ihr "OnlyPID" (1) oder den "Vollausbau" mit den Relais nutzt (0).

ONLYPIDSCALE (1) erlaubt es beim OnlyPID (1) auch die Waage zu nutzen. 

BREWMODE definiert, ob ihr nur das Ventil und die Pumpe steuert (1) oder auch eine Waage verbaut habt (2). Dazu wird in der Zukunft im Handbuch noch mehr stehen.

BREWDETECTION Diese ist hier [Brüherkennung](https://manual.rancilio-pid.de/de/customization/brueherkennung.html) genauer erläutert. Knapp zusammengefasst,
definiert ihr hier, ob diese per Software (1) , Brühschalter beim Vollausbau (2) oder per Sensor bei OnlyPid (3) erkannt werden soll. 

COLDSTART_PID gibt an, ob ihr Standard Kaltstart Parameter nehmen wollt. Diese sind durchschnittliche Werte, welche für eine Rancilio und Gaggia funktionieren sollen. Wenn ihr euch selber daran probieren wollt wählt ihr (2). Dazu hier mehr zum [Kaltstart](https://manual.rancilio-pid.de/de/customization/pid-werte.html#kaltstart)

TRIGGERTYPE HIGH es gibt LOW UND HIGH Trigger für das Ventil/Pumpe. Dies wird hier definiert.

VOLTAGESENSORTYPE und PINMODEVOLTAGESENSOR ist für die Konfiguration vom Voltagesensor hier dazu mehr: [Brüherkennung bei Only PID](
https://manual.rancilio-pid.de/de/customization/brueherkennung.html#sensor-zur-brüherkennung-bei-only-pid

## TOF sensor for water level

```
#define TOF 0                      // 0 = no TOF sensor connected; 1 = water level by TOF sensor
#define TOF_I2C 0x29               // I2C address of TOF sensor; 0x29 by default
#define CALIBRATION_MODE 0         // 1 = enable to obtain water level calibration values; 0 = disable for normal PID operation; can also be done in Blynk
#define WATER_FULL 102             // value for full water tank (=100%) obtained in calibration procedure (in mm); can also be set in Blynk
#define WATER_EMPTY 205            // value for empty water tank (=0%) obtained in calibration procedure (in mm); can also be set in Blynk
```
Habt ihr keinen TOF Sensor, könnt ihr diesen Teil ignorieren und TOF (0) einstellen.  

## E-Trigger
```
#define ETRIGGER 0                 // 0 = no trigger (for Rancilio except Rancilio E), 1 = trigger for CPU of Rancilio E
#define ETRIGGERTIME 60            // seconds, time between trigger signal
#define TRIGGERRELAYTYPE HIGH      // LOW = low trigger, HIGH = high trigger relay for E-Trigger
```
Die Silvia E hat ein Energiesparmodul, dieses kann überbrückt werden mit einem Relais. Dieses kann hier definiert werden, wenn ETRIGGER (1) gewählt wird.
Der zugehörige PIN wird später definiert, im Abschnitt PIN Layout.

ETRIGGERTIME ist die Zeitdauer zwischen den Signalen.

TRIGGERRELAYTYPE ist der Relaistyp (High oder LOW).

## Weight SCALE
```
#define WEIGHTSETPOINT 30          // Gramm 
```
Hier wird mit WEIGHTSETPOINT das Sollgewicht für die Waage definiert.

##  Wifi 
```
#define HOSTNAME "rancilio"
#define D_SSID "myssid"
#define PASS "mypass"
#define MAXWIFIRECONNECTS 5        // maximum number of reconnection attempts, use -1 to deactivate
#define WIFICINNECTIONDELAY 10000  // delay between reconnects in ms
```
HOSTNAME ist der Hostname der Maschine,
D_SSID und PASS sind die Wlan Einstellungen. 

MAXWIFIRECONNECTS definiert wie viele Reconnect gemacht werden, bis der Fallback aktiviert wird (bei Start der Maschine) oder bis der Offline Modus aktiviert wird (nach dem erfolgreichen Start)

WIFICINNECTIONDELAY ist die Zeitspanne bis der nächste Reconnect probiert wird. 

## OTA
```
#define OTA true                   // true = OTA activated, false = OTA deactivated
#define OTAHOST "rancilio"         // Name to be shown in ARUDINO IDE Port
#define OTAPASS "otapass"          // Password for OTA updtates
```

## MQTT
```
#define MQTT 0                     // 1 = MQTT enabled, 0 = MQTT disabled
#define MQTT_USERNAME "mymqttuser"
#define MQTT_PASSWORD "mymqttpass"
#define MQTT_TOPIC_PREFIX "custom/Küche."  // topic will be "<MQTT_TOPIC_PREFIX><HOSTNAME>/<READING>"
#define MQTT_SERVER_IP "XXX.XXX.XXX.XXX"  // IP-Address of locally installed mqtt server
#define MQTT_SERVER_PORT 1883    
```

## Blynk
```
#define AUTH "myauth"
#define BLYNKADDRESS "blynk.clevercoffee.de"  // blynk-server IP-Address
#define BLYNKPORT 8080             // blynk-server portver 
```

## PID - offline values
```
#define SETPOINT 95                // Temperatur setpoint
#define STEAMSETPOINT 120          // Temperatur setpoint
#define AGGKP 69                   // Kp normal
#define AGGTN 399                  // Tn
#define AGGTV 0                    // Tv

// PID coldstart
#define STARTKP 50                 // Start Kp during coldstart
#define STARTTN 150                // Start Tn during cold start

// PID - offline brewdetection values
#define AGGBKP 50                  // Kp
#define AGGBTN 0                   // Tn 
#define AGGBTV 20                  // Tv
```

## Backflush values
```
#define FILLTIME 3000              // time in ms the pump is running
#define FLUSHTIME 6000             // time in ms the 3-way valve is open -> backflush
#define MAXFLUSHCYCLES 5           // number of cycles the backflush should run, 0 = disabled
```
## Pin Layout
```
#define ONE_WIRE_BUS 2             // Temp sensor pin
#define PINBREWSWITCH 0           // 0: A0 Analog PIN ; >0 : DIGITAL PIN, ESP8266: ONLY USE PIN15 AND PIN16! 
#define pinRelayVentil 12          // Output pin for 3-way-valve
#define pinRelayPumpe 13           // Output pin for pump
#define pinRelayHeater 14          // Output pin for heater
#define PINVOLTAGESENSOR  15       //Input pin for volatage sensor
//#define OLED_RESET 16            // Output pin for dispaly reset pin
#define PINETRIGGER 16             // PIN for E-Trigger relay
#define STEAMONPIN 17              // STEAM active
#define OLED_SCL 5                 // Output pin for dispaly clock pin
#define OLED_SDA 4                 // Output pin for dispaly data pin
#define HXDATPIN 99                // weight scale PIN 
#define HXCLKPIN 99                // weight scale PIN  
#define SCREEN_WIDTH 128           // OLED display width, in pixels
#define SCREEN_HEIGHT 64           // OLED display height, in pixels  
```

## Historic (no settings)
```
#define PONE 1                     // 1 = P_ON_E (default), 0 = P_ON_M (special PID mode, other PID-parameter are needed)
#define TEMPSENSOR 2               // 2 = TSIC306 1=DS18B20
```

## Historic (no settings)
```
#if (defined(ESP8266) && ((PINBREWSWITCH != 15 && PINBREWSWITCH != 0 && PINBREWSWITCH != 16 )))
  #error("WRONG Brewswitch PIN for ESP8266, Only PIN 15 and PIN 16");  
#endif
```

#endif // _userConfig_H
```

## Code hochladen

Wenn ihr die .ino Datei öffnet, öffnet sich automatisch im zweiten Tab die userConfig.h mit den wichtigen Einstellungen. Danach auf den Pfeil klicken für den Upload auf den Microkontroller. Achtet darauf, dass Ihr den Auth-Code der Blynk-App und die WLAN-Zugangsdaten im Code der userConfig.h hinterlegt habt.

![](../img/image-2.png)

Bitte achtet vorher drauf, dass Ihr in den Board Einstellungen den richtigen COM Port ausgewählt habt.

Diesen könnt ihr auch auch im Gerätemanager prüfen (falls ihr ihn nicht wisst):

![](../img/34.png)

![](../img/35.png)

## Testen

Wenn alles geklappt habt könnt ihr auf dem Serial Monitor erkennen, wie sich der Microkontroller mit Blynk verbindet.

![](../img/36.png)

Klappt das und ist der Temperatursensor korrekt angeschlossen seht ihr am Handy in der Blynk App die Raumtemperatur.
Jetzt könnt iht nach und nach die anderen Bauteile verbinden (Relais) und weiter testen.

### OTA

Hier wird der Update **O**ver **T**he **A**ir eingestellt.

Dafür muss die Maschine eingeschalten sein und sich euer Rechner (mit Arduino) im selben WLAN Netz befinden. Dann erscheint unter Werkzeuge > Port <aktuelle Auswahl> > Netzwerkschnittstellen "Rancilio <IP-Addresse>". Wählt diesen Port aus und lädt den Code entsprechend hoch.

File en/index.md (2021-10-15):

---
layout: default
title: EN - Manual
has_children: true
nav_order: 2
---

## Manual (english)

This is the manual for the Rancilio PID project. It covers all the steps necessary for your own build.

We recommended you read the introduction. It explains the requirements to a successful upgrade of your machine with a PID. It describes as well the abilities and limitations of the PID. The first step towards your own PID is procuring the parts as per the provided list, depending on what functionality you want and what equipment is available. While you are waiting for the parts to come, there is time to install and set up the required software. Once the parts are assembled, the controller is flashed with the current software and everything is installed into your espresso machine. After successful initial testing you will find many customization options in the last chapter of the manual.

More information is available at the [Rancilio PID Website](http://rancilio-pid.de/).

## Contact
Join the [Chat-Server](https://chat.rancilio-pid.de/). It has a tendency to be mostly German, but English is welcome.

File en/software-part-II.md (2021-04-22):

---
layout: default
title: Software Part II
parent: EN - Manual
has_children: false
nav_order: 4
---

# Software Teil II
{: .no_toc }

Contents

* TOC
{:toc}

## Introduction

In this chapter we will explain how to get the program code onto your NodeMCU. You can start with that as soon as you have you Microcontroller at hand, no other parts are needed. For later testing, you will however need at least the temperature sensor

## Open the program in Arduino IDE

In the current release there are (among others) two files:
* rancilio-pid.ino
* userConfig.h

rancilio-pid.ino contains the actual program while userConfig.h holds all user specific configuration options.

When you open the .ino file, the other files which belond to the project are automatically opend in separate tabs within Arduino IDE and can be edited and saved directly from here.

### Preferences

The most important functions have to be parameterized in userConfig.h. Please remember to set the correct PID mode, temperature sensor and possibly display.

```
// Display -> siehe ./customization/Displey.md
#define DISPLAY 2            // 2 = Defaulf AZDelivery Display
#define DISPLAYTEMPLATE 1    // 1: Standard Display Template, 2: Minimal Template
#define MACHINELOGO 1        // 1 = Rancilio, 2 = Gaggia
#define DISPALYROTATE U8G2_R0   // rotate display clockwise: U8G2_R0 = no rotation; U8G2_R1 = 90°; U8G2_R2 = 180°; U8G2_R3 = 270°
#define SHOTTIMER  1 // 0: no SHOTTIMER, 1: SHOTTIMER

// Wlan and Connection
#define OFFLINEMODUS 0       // 0 = Blynk and WIFI are used; 1 = offline mode (only preconfigured values in code are used!)
#define FALLBACK 1           // 1 = fallback to values stored in eeprom, if blynk is not working; 0 = deactivated
#define OTA true             // true = activate update via OTA
#define MQTT 0               // 1 = MQTT enabled, 0 = MQTT disabled
#define GRAFANA 1            // 1 = grafana visualisation. Access required, 0 = off (default)
#define MAXWIFIRECONNECTS 5  // maximum number of reconnects; use -1 to set to maximum ("deactivated")
#define WIFICINNECTIONDELAY 10000 // delay between reconnects in ms

// PID & Hardware
#define ONLYPID 1            // 1 = Only PID, no preinfusion; 0 = PID and preinfusion
#define BREWDETECTION 1      // 0 = off; 1 = Software; 2 = Hardware
#define COLDSTART_PID 1     // 1 = default COLDStart Values , 2 = eigene Werte via Blynk, Expertenmodusaktiv
#define TRIGGERTYPE HIGH     // LOW = low trigger, HIGH = high trigger relay

//E-Trigger
#define ETRIGGER 0  // 0: no Trigger (for Raniclio without E) 1: Trigger for CPU of Rancilio E
#define ETRIGGERTIME 60 // Seconds, time between for Trigger Signal
#define PINETRIGGER 16 // Pin for Etrigger Relay
#define TRIGGERRELAYTYPE HIGH  // LOW = low trigger, HIGH = high trigger relay for ETrigger

// Wifi -> Infos siehe unten
#define HOSTNAME "Rancilio"
#define D_SSID "myssid"
#define PASS "mypass"

// OTA -> siehe unten
#define OTAHOST "Rancilio"   // Name to be shown in ARUDINO IDE Port
#define OTAPASS "otapass"    // Password for OTA updtates

//MQTT
#define MQTT_USERNAME "myuser"
#define MQTT_PASSWORD "mypass"
#define MQTT_TOPIC_PREFIX "custom/Küche."  // topic will be "<MQTT_TOPIC_PREFIX><HOSTNAME>/<READING>"
#define MQTT_SERVER_IP "XXX.XXX.XXX.XXX"       // IP-Address of locally installed mqtt server
#define MQTT_SERVER_PORT 1883    

// BLynk
#define AUTH "myauth"
#define BLYNKADDRESS "blynk.clevercoffee.de"         // IP-Address of used blynk server
#define BLYNKPORT 8080  //Port for blynk server

//PID - offline values
#define SETPOINT 95  // Temperatur setpoint
#define AGGKP 69     // Kp Normal
#define AGGTN 399    // Tn
#define AGGTV 0      // Tv

// PID Coldtart
#define STARTKP 50   // Start Kp during coldstart
#define STARTTN 150  // Start Tn during cold start

//PID - values for offline brewdetection
#define AGGBKP 50    // Kp
#define AGGBTN 0   // Tn
#define AGGBTV 20    // Tv

//backflush values
#define FILLTIME 3000       // time in ms the pump is running
#define FLUSHTIME 6000      // time in ms the 3-way valve is open -> backflush
#define MAXFLUSHCYCLES 5      // number of cycles the backflush should run; 0 = disabled

//PIN BELEGUNG
#define ONE_WIRE_BUS 2  // TEMP SENSOR PIN

#define pinRelayVentil    12    //Output pin for 3-way-valve
#define pinRelayPumpe     13    //Output pin for pump
#define pinRelayHeater    14    //Output pin for heater

//#define OLED_RESET 16     //Output pin for dispaly reset pin
#define OLED_SCL 5        //Output pin for dispaly clock pin
#define OLED_SDA 4        //Output pin for dispaly data pin
#define SCREEN_WIDTH 128 // OLED display width, in pixels
#define SCREEN_HEIGHT 64 // OLED display height, in pixels  

// Historic, no settings
#define PONE 1               // 1 = P_ON_E (default), 0 = P_ON_M (special PID mode, other PID-parameter are needed)
#define TEMPSENSOR 2         // 2 = TSIC306

```

### Wifi

Under Wifi please specify the desired hostname of the NodeMCU, the SSID to connect to and the according Wifi password. Please also check that your SSID doesn't contain any blank spaces or special characters as those often lead to problems.

```
#define HOSTNAME "Rancilio"

#define D_SSID "wifiname"

#define PASS "wifipass"
```

### Blynk

Under Blynk, enter your Auth token from Part 1 as AUTH.

```
#define AUTH "myauth"
#define BLYNKADDRESS "blynk.clevercoffee.de"         // IP-Address of used blynk server
#define BLYNKPORT 8080  //Port for blynk server

```

### PID

Here you can define your initial PID values or just start with the "factory defaults"

### OTA

Here, **O**ver **T**he **A**ir update is set up. This is important once your NodeMCU is buried deep in your machine and you want to update to a new software version.

## Flashing the code

Make sure the Auth token as well as the Wifi data you have entered is correct.



Also make sure you have chosen the right COM port for flashing. If you are unsure, you can check the COM port number in device manager





Next, click on the arrow symbol to start the upload to the Microcontroller

## Testing

If everything has worked fine, you can see the communication between your NodeMCU and Blynk in the Serial Monitor



If that has worked and if you already have a temperature sensor connected, you can see you current room temperature in the Blynk app. Now you can start adding more and more parts to you setup, like the SSR or a display and continue testing.

### perform OTA update (optional)

In order to do an OTA update, the machine has to be turned on and has to be in the same network as your PC running Arduino IDE. You will now see your NodeMCU under Tools > Port > Network > "Hostname <IP-Address>". Choose this entry and start flashing the software just as before.

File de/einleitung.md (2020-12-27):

---
title: Einleitung PID System
parent: DE - Handbuch
has_children: false
nav_order: 3
---

# Einleitung PID System
{: .no_toc }

Inhaltsverzeichnis

* TOC
{:toc}

## Was bringt mir eine PID-Steuerung?

Eine PID-Steuerung ermöglicht es deiner Espressomaschine die Temperatur des Brühwassers sehr viel exakter und konstanter zu regeln als das mit den werksseitig verbauten Bimetall-Thermostaten möglich ist.

Die gängigen Thermostate haben eine Schwankung der durch sie geregelten Temperatur von bis zu 10°, auch Hysterese genannt. Grob gesagt bedeutet das: eure Maschine heizt hoch, bis der Thermostat seine Schalttemperatur erreicht hat und den Strom zur Heizung unterbricht. Gleichzeitig leuchtet die Lampe eurer Maschine auf und zeigt euch Brühbereitschaft an.

Jetzt verliert der Kessel eurer Maschine je nach Ausführung mehr oder weniger schnell Wärmeenergie durch Abstrahlung an die Umgebung. Dies geschieht so lange, bis der Anschaltpunkt des Thermostaten erreicht ist und er den Stromkreis zur Heizung wieder aktiviert. Die Brühlampe eurer Maschine erlischt und die Maschine heizt wieder hoch bis zum Erreichen des Abschaltpunktes.

Zwischen diesen beiden Temperaturpunkten leuchtet die ganze Zeit die Brühbereitschaftslampe eurer Maschine. Die wirkliche Brühtemperatur des Wassers kann sich aber entweder ganz unten nah beim Anschaltpunkt des Thermostaten befinden, oder ganz oben kurz vor dem Abschaltpunkt, oder irgendwo im Bereich dazwischen.

Beim Espresso ziehen ist die Temperatur des Brühwassers einer DER entscheidenden Faktoren für den Geschmack des Kaffees. Schon eine Differenz von 1° kann den Unterschied zwischen sauer (zu kalt), verbrannt (zu heiß) oder lecker (genau richtig) bedeuten. Das hängt jeweils stark von der verwendeten Bohne ab.

Eine Maßnahme ist das sogenannte Temperatursurfen, eine relativ aufwendige manuelle Methode der Temperaturkontrolle die es erfordert, dass der Bediener tatsächlich an der Maschine steht.

Viele Nutzer sind davon irgendwann genervt, wir waren es genauso.

Die Lösung für kleinere Einkreiser-Maschinen ist, den Thermostaten der Maschine aus dem Spiel zu nehmen und einen PID-Regler zu verbauen. Dieser regelt die Brühtemperatur mit einer Schwankung von deutlich unter 1°, unser System kann auf bis zu 0,1° genau regeln. Man muss nicht mehr an der Maschine bleiben um den richtigen Zeitpunkt zum Bezug zu treffen, der richtige Zeitpunkt ist ab jetzt einfach immer sobald die Maschine einmal durchgeheizt ist!

## Was kann unser System?

Folgende Eckdaten zeichnen unseren DIY PID aus:

* Regelung der Brühtemperatur mit einer Genauigkeit von bis zu +/- 0,1°
* Steuerung der Brühzeit inkl. Pre-Infusion in der Ausbaustufe „Vollausbau“ möglich
* Bedienung über eine Smartphone-App (iOS & Android)
* Datenmonitoring über Grafana (webbasiert) und MQTT (IoT) möglich
* Updates der PID-Software sind drahtlos über WLAN möglich
* Unsere PID-Software ist OpenSource: für euch kostenfrei und auf persönliche Anforderungen anpassbar
* Geringer Platzbedarf, passt problemlos in die meisten kleineren Espressomaschinen
* Die serienmäßige Verkabelung der Maschine bleibt erhalten und wird nur erweitert. Die Maschine kann nach dem Umbau problemlos wieder zurückgerüstet werden.
* Aktive User-Community im Projektchat mit schnellem Support
* Anregungen zur Weiterentwicklung der Software werden von uns gerne aufgenommen. User-Input ist immer willkommen und bringt den PID weiter!

## Universell – Umgebaute Maschinentypen

Entwickelt wurde unser System ursprünglich an einer Rancilio Silvia, es ist aber universell einsatzbar. Bislang haben unsere User die folgenden Maschinen erfolgreich umgebaut:

  Rancilio Silvia V1 – V5
  Gaggia Classic (9303) / Classic Pro (9480)
  Lelit PL41 / PL42
  La Pavoni EPL / Saeco Aroma / Gaggia New Classic (9403)
  E61 Einkreiser (Bazzar A1 Livello, Fiorenzato Colombina)
  E61 Zweikreiser (Profitec Pro500)

## Aufbau / Unterschiede PID Only vs. Vollausbau

Grundsätzlich besteht unser PID-Regler aus den folgenden Komponenten:

ID | Erklärung
-|-
1 | Mikrocontroller NodeMCU V2                 
2 | Temperatursensor TSIC 306                 
3 | Solid State Relais (SSR)                       
4 | Netzteil zur Stromversorgung               
5 | Display (empfohlen, aber optional)      

Trockenaufbau

Es gibt zwei verschiedene Ausbaustufen unseres Systems: PID Only und den erweiterten Vollausbau.

## Grundversion (PID Only)

Die Grundversion ist ein klassischer PID-Regler: der Temperatursensor nimmt die aktuelle Temperatur des Kessels auf (Input) und gibt den Wert an die PID-Software auf den Mikrocontroller ( auch NodeMCU genannt) weiter. Diese gibt dann das Regler-Signal (Output) an das SSR aus, welches die Heizung eurer Maschine aktiviert bzw. deaktiviert.

Damit habt ihr eine exakte Regelung der Brühtemperatur auf euren Wunschwert durch die PID-Software, die restliche Bedienung eurer Maschine bleibt unangetastet. MQTT, Displayausgabe und Handy Steuerung geht auch bei Only PID

## Vollausbau

Beim Vollausbau gehen wir einen Schritt weiter und überlassen die Ansteuerung der Pumpe und des Magnetventils ebenfalls der Software. Dadurch könnt ihr in der App 3 Zeitintervalle vorgeben:

* Pre-Infusion: die Pumpe baut Druck auf + das Magnetventil gibt das Brühwasser auf den Siebträger

* Pause: die Pumpe pausiert, der aufgebaute Druck bleibt aber durch das aktivierte MV im Siebträger bestehen. So wird der Kaffeepuck gleichmäßig durchfeuchtet, z. B. kann so Channeling reduziert werden.

* Brühzeit: jetzt startet der „normale“ Bezug mit der von dir festgelegten Bezugszeit, z. B. 25 Sekunden. Je nach Bohnensorte und persönlichem Geschmack kann eine kürzere oder längere Bezugszeit den Geschmack des Espressos noch mehr nach vorne bringen.

Beim Vollausbau ändert sich die Bedienung eurer Maschine auch etwas: der Brühschalter, mit dem ihr bislang den Bezug gestartet und auch wieder gestoppt habt, dient nun nur noch als Taster, der den automatisierten Bezug startet. Gestoppt wird der Bezug durch die Software, auch wenn der Schalter noch auf ON steht.

Unsere Empfehlung, basierend auf unseren eigenen Erfahrungen und denen der bislang mehr als 250 User des PIDs, lautet ganz klar, zuerst die Grundversion PID-Only umzusetzen. Damit ist die größte geschmackliche Verbesserung im Vergleich zum vorherigen Serienzustand eurer Maschine zu erwarten. Der Vollausbau ist darauf aufbauend eine Erweiterung der Möglichkeiten, aber gleichzeitig auch ein komplexerer Umbau.

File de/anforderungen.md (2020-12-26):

---
title: Anforderungen an dich
parent: DE - Handbuch
has_children: false
nav_order: 2
---

# Anforderungen an dich – Warnhinweis
{: .no_toc }

Inhaltsverzeichnis

* TOC
{:toc}

## Warnhinweis

> {{ site.warnhinweis }}

## Zentrale Fragen

### Traue ich mir zu mit 230V Spannung zu arbeiten? Ist mir die Gefahr bewusst?

Ihr verändert bzw. erweitert mit dem Einbau die werksseitige 230V Verkabelung der Maschine. Damit habt ihr immer das Risiko eines lebensgefährlichen Stromschlags, sei es durch Fehler beim Einbau, nicht ausreichend isolierte Kontakte, brüchige Isolierung bei älteren Kabeln, etc. **Das muss euch bewusst sein, ihr macht den Einbau auf eigenes Risiko!**

Wenn ihr das nicht fachlich richtig umsetzen könnt oder unsicher seid, sucht euch bitte jemanden vom Fach! Für jemanden mit Grundwissen in Elektrotechnik ist der Einbau kein Problem. Wir helfen bei konkreten Fragen gerne weiter, aber die Verantwortung für euren Umbau können und wollen wir euch nicht abnehmen!

Eine eventuell noch bestehende Garantie bei neueren Maschinen ist durch den Einbau selbstverständlich erloschen, das muss euch ebenfalls bewusst sein.

### Habe ich Lust dazu, mich näher mit meiner Maschine und mit der PID-Steuerung zu beschäftigen?

Mit der PID-Steuerung erhöht ihr die Komplexität eurer Maschine. Ihr hab jetzt mehr Möglichkeiten, für den Kaffeegenuss relevante Parameter zu verändern als vorher. Das kann viel Freude machen, kann aber auch überfordern, sofern man beim ausprobieren nicht planvoll vorgeht.

Wir haben für die gängigen Einkreiser-Espressomaschinen bereits gut funktionierende Parameter-Setups verfügbar, daher werden sich die Ergebnisse in der Tasse verbessern, auch wenn ihr „nur“ den PID installiert und die Standardparameter aufspielt.       

Ihr kommt aber zu noch besseren Ergebnissen, wenn ihr etwas besser Bescheid wisst was der PID tut und warum er das tut. Es lohnt sich die Zeit zu investieren um a) seine Maschine besser kennen zu lernen und b) die Grundfunktion des PIDs zu verstehen.

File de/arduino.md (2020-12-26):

---
title: Arduino IDE einrichten
parent: DE - Handbuch
has_children: false
nav_order: 6
---

# Arduino IDE einrichten
{: .no_toc }

Inhaltsverzeichnis

* TOC
{:toc}

## Installationsvideo

In diesem kurzen Video erklären wir die Installation der Arduino IDE und zeigen wie unsere OpenSource Software Rancilio-PID auf dem NodeMCU installiert wird. Viel Spaß!

Installationsvideo (https://www.youtube.com/watch?v=w7vBGSVWPrw)

## Download

Wird benötigt, um den Code auf den Controller zu spielen.

[Link zu Arduino](https://www.arduino.cc/en/Main/Software)

Screenshot der Arduino Homepage

## Der Programmcode

Download des aktuellen Programmcode findest du im aktuellen Release.

[Link zum Github Repository](https://github.com/rancilio-pid/ranciliopid/releases)

Screenshot der Github Homepage

## Installation der Arduino IDE

Arduino Installation

Hinweise zur Installation befinden sich auf der [Arduino Homepage](https://www.arduino.cc/en/Guide).

Nach der erfolgreichen Installation kann Arduino über das Startmenü gestartet werden.

## Arduino Voreinstellungen

### Boardverwaltungs-URL anlegen

Wir benötigen für den Einsatz des NodeMCUs eine zusätzliche Boardverwaltungs-URL.

Diese erreicht ihr unter: Datei > Voreinstellungen

| Key | Value |
|-|-|
| Boardverwaltungs-URL | `http://arduino.esp8266.com/stable/package_esp8266com_index.json`|

<details markdown="block">
  <summary> Windows </summary>

  Windows Arduino Voreinstellungen

</details>

<details markdown="block">
  <summary> Linux (Ubuntu) </summary>

  Linux (Ubuntu)

</details>

### Boardtreiber installieren

Als nächstes müssen die ESP8266 Boardtreiber installiert werden.

Dies erreicht ihr unter: Werkzeuge > Board: "[\<Version\>]" > Boardverwalter...

<details markdown="block">
  <summary> Windows </summary>

  Windows Arduino Boardverwalter

</details>

<details markdown="block">
  <summary> Linux (Ubuntu) </summary>

  Linux (Ubuntu) Boardverwalter

</details>

Bitte die aktuelle Version installieren.

Typ \<Alle\> > "esp": "**esp8266** by **ESP8266 Community**"

ESP8266 installieren

Nun ist die Arduino IDE vorbereitet. Weiter geht es mit den Bibliotheken.

## Bibliotheken installieren

Der sicherste und einfachste Weg alle Bibliotheken korrekt zu installieren, ist es, die [Bibliotheken aus Github](https://github.com/rancilio-pid/ranciliopid/tree/master/rancilio-pid/libraries) zu nehmen. Diese solltet ihr bereits heruntergeladen haben (siehe [Programmcode](#der-programmcode)). Kopiert die kompletten Ordner einfach in den Arduino Libraries Ordner zu kopieren:

| OS | Arduino Libraries Ordner |
|-|-|
| Windows | `My Documents\Arduino\libraries\` |
| OSX | `~/Documents/Arduino/libraries/` |
| Linux |`~/Arduino/libraries`|

Wie immer ist es empfehlenswert beim offiziellen Guide mehr Infos einzuholen: [Link](https://www.arduino.cc/en/Guide/Libraries).

### Bibliotheken manuell installieren

Alternativ müssen folgende Libraries per Hand installiert werden:

* Blynk
* TimeLib
* WidgetRTC
* U8x8lib
* OneWire
* DallasTemperature
* PID_v1.h

Die Installation der einzelnen Bibliotheken erfolgt wieder über die Verwaltung in Arduino IDE:

Bibliotheken verwalten

<details markdown="block">
  <summary> OneWire </summary>

  
</details>

<details markdown="block">
  <summary>
    DallasTemperature
  </summary>


</details>

<details markdown="block">
  <summary> U8x8lib </summary>

  1. Geht auf [https://github.com/olikraus/u8g2](https://github.com/olikraus/u8g2)
  1. Code > Download Zip
  
  1. Legt die Dateien im [Arduino Libraries Ordner](#bibliotheken-installieren) ab
  1. Erstellen einen Ordner: `U8x8lib`
  1. Den Inhalt aus dem ZIP File Ordner: u8g2-master.zip\u8g2-master\cppsrc  UND csrc in den neu erstellten Ordner kopieren (ja, es sind eine ganze Menge Dateien :))
  
    
</details>

<details markdown="block">
  <summary> PID_v1.h </summary>

  1. Geht auf [https://github.com/br3ttb/Arduino-PID-Library](https://github.com/br3ttb/Arduino-PID-Library)
  1. Code > Download Zip  
  
  1. Legt die Dateien im [Arduino Libraries Ordner](#bibliotheken-installieren) ab
  1. Erstellen einen Ordner: `PID_v1`
  1. Die vier Dateien aus dem ZIP File kopieren und in den neuen Ordner einfügen:
  
    
</details>

<details markdown="block">
  <summary> Blynk </summary>

  1. Geht auf [https://www.blynk.cc/getting-started/](https://www.blynk.cc/getting-started/)
  
  1. Geht auf [https://github.com/blynkkk/blynk-library/releases/tag/v0.5.4](https://github.com/blynkkk/blynk-library/releases/tag/v0.5.4)
  
  
  
  
  1. Wechseln in den [Arduino Libraries Ordner](#bibliotheken-installieren)
  
    
</details>

## Board einstellen




Wenn alle Bibliotheken installiert sind, müsste es wie folgt aussehen:



Somit ist alles nun für das Einrichten von Blynk und das Flashen von dem Code vorbereitet. Dann kann der erste Test beginnen.

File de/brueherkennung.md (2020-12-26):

---
title: Brüherkennung
parent: DE - Handbuch
has_children: false
nav_order: 11
---

# Der Einbau
{: .no_toc }

Inhaltsverzeichnis

* TOC
{:toc}

## Einleitung

Wie in dem vorherigen Kapitel erwähnt, soll der brew heater detection limit Wert auf „0“ gestellt werden, um diesen bei dem ersten Test zu deaktivieren. Wenn der normale PID gut läuft, ein für dich angenehmes Heizverhalten sich beim Starten zeigt und stabil am Soll-Wert läuft, dann kannst du die Brüherkennung dir genauer anschauen.

## Funktionsweise

Ohne zu tief in die technischen Details der Erkennung einzusteigen, soll dir dennoch kurz die grundlegende Funktionsweise erläutert werden. Der Mikrocontroller überwacht kontinuierlich die Temperatur. Dabei wird die zeitliche Veränderung der Heizrate/Kühlrate für fortlaufend Zeitfenster analysiert. Das Ergebnis ist dann die „heat average“. Wenn diese negativ wird, kühlt die Maschine ab, bei einem Hochheizen wird diese positiv.

Brüherkennung

Die Brüherkennung „horcht“ nun auf dieser „heat average“, in dem der negative Grenzwert definiert wird, ab dem die Maschine von einem Bezug ausgehen soll. Dieser wird bei „brew heater detection limit“ definiert. Hierbei ist zu beachten, dass hier der absolute Werte eingetragen wird: 70 entspricht -70. Die Übersetzung in den negativen Wert erfolgt im Quellcode!

Vereinfacht kann festgehalten werden, dass die „brew heater detection limit“ letztendlich die Empfindlichkeit der Erkennung wiedergibt: Je kleiner der Wert ist, je empfindlicher reagiert die Brüherkennung. Wenn die zu empfindlich (kleiner Wert, z.B. 5) ist, wird jedes normale Abkühlung als Brühvorgang erkannt, ist der Wert zu groß (z.B. 1000) wird erst zu spät oder gar nicht die Brüherkennung ausgelöst. Es kann dazu hilfreich sein den Verlauf der heat average über eine längere Zeit zu beobachten und somit einen geeigneten Werte zu finden.

Wenn die Erkennung ausgelöst werden, dann gelten für den definierten Zeitraum in „brew timer Software Seconds“ (im oberen Screenshot, 120 Sekunden) andere PID Werte. Somit kann der Regler nun aggressiver auf den Brühvorgang reagieren und schneller hochheizen. Wichtig ist hierbei, dass jede Unterschreitung des Grenzwertes zu einer Auslösung der Erkennung führt. Der Verlauf nach dem Auslösen wird nicht weiter ausgewertet, sondern die geänderten PID Werte gelten fix für die definierte Zeit.

## PID Werte

Für den kurzen Zeitraum muss der PID schnell wieder auf Temperatur kommen, ohne überzuschwingen. Hierzu muss vor allem der I-Anteil erhöht werden, damit sich der Regler nicht die erfolgte Abweichung vom Soll-Wert für die Zukunft „merkt“. Der D-Anteil kann auch erhöht werden, um den Regler beim Abfallen der Temperatur zu „beschleunigen“ und „abzubremsen“, wenn die Temperatur wieder Richtung Soll-Wert geht. Als Größenordnung können die Werte aus dem oberen Screenshot genommen werden.
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

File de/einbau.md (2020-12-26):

---
title: Der Einbau
parent: DE - Handbuch
has_children: false
nav_order: 9
---

# Der Einbau
{: .no_toc }

Inhaltsverzeichnis

* TOC
{:toc}

## Warnhinweis

> {{ site.warnhinweis }}

## Einleitung

Wenn der Test erfolgreich war, kannst du beginnen deinen Einbau zu planen. Je nach Ausbaustufe musst du nur das Netzteil und Controller mit Strom versorgen, den Temperatursensor einbauen am Kessel. Wir zeigen dir hier am Beispiel der Rancilio Siliva wie der Umbau gelingt. Weiter Maschinen, wie z.B. die Gaggia wurde auch schon erfolgreich umgebaut.

## Originaler Schaltplan

Der erste Schaltplan zeigt den original Zustand der Silvia vor dem Umbau.

Org Schaltplan
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

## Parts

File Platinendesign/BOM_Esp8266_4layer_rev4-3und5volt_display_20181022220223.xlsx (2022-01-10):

ID | Name | Designator | Footprint | Quantity | Manufacturer Part | Manufacturer | Supplier | Supplier Part | Mounted
1 | DIP-1X15P2.54 | U1,U2,U5,U3 | DIP-1X15P2.54 | 4 | 220S-1*15P H=8.5MM Ytype Gold-plated | Ckmtw | LCSC
2 | PH-2AW | Analog_In,Supply | PH-2AW | 2 | PH-2AW RHOS | BOOMELE | LCSC
3 | PH-4AW | Pin15,Pin13,Pin12,Pin2,Pin14 | PH-4AW | 5 | PH-4AW | BOOMELE | LCSC
4 | PH-5AW | Display | PH-5AW | 1 | PH-5AW | BOOMELE | LCSC

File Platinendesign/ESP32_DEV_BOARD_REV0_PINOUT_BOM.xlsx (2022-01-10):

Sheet: PIN_Belegung
ESP32-PinOuts für Clevercoffee-PID
GPIO | Input | Output | Notes | Modul | Elektr. Bauteil | GND | 5V | 3,3V | ADC-Version | PCB? | GPIO | Input | Output | Notes | Referenzdesign
0 | pulled up | OK | outputs PWM signal at boot |  |  |  |  |  | ADC2 |  | 0 | pulled up | OK | outputs PWM signal at boot
1 | TX pin | OK | debug output at boot |  |  |  |  |  |  |  | 1 | TX pin | OK | debug output at boot
2 | OK | OK | connected to on-board LED |  |  |  |  |  | ADC2 |  | 2 | OK | OK | connected to on-board LED
3 | OK | RX pin | HIGH at boot | Button | Push Button |  |  | 3,3V |  | nein | 3 | OK | RX pin | HIGH at boot
4 | OK | OK |  | Dampfschalter | Schalter |  |  |  | ADC2 | nein | 4 | OK | OK
5 | OK | OK | outputs PWM signal at boot |  |  |  |  |  |  | nein | 5 | OK | OK | outputs PWM signal at boot
6 | x | x | connected to the integrated SPI flash | n.v. | n.v. | n.v. | n.v. | n.v. | n.v. |  | 6 | x | x | connected to the integrated SPI flash
7 | x | x | connected to the integrated SPI flash | n.v. | n.v. | n.v. | n.v. | n.v. | n.v. |  | 7 | x | x | connected to the integrated SPI flash
8 | x | x | connected to the integrated SPI flash | n.v. | n.v. | n.v. | n.v. | n.v. | n.v. |  | 8 | x | x | connected to the integrated SPI flash
9 | x | x | connected to the integrated SPI flash | n.v. | n.v. | n.v. | n.v. | n.v. | n.v. |  | 9 | x | x | connected to the integrated SPI flash
10 | x | x | connected to the integrated SPI flash | n.v. | wäre ein | n.v. | n.v. | n.v. | n.v. |  | 10 | x | x | connected to the integrated SPI flash
11 | x | x | connected to the integrated SPI flash | n.v. | n.v. | n.v. | n.v. | n.v. | n.v. |  | 11 | x | x | connected to the integrated SPI flash
12 | OK | OK | boot fail if pulled high | Rotary Encoder / Touch | Rotary Encoder Push Button |  |  |  | ADC2 | ja | 12 | OK | OK | boot fail if pulled high
13 | OK | OK |  | Touch (Optional) |  |  |  |  |  | ja | 13 | OK | OK
14 | OK | OK | outputs PWM signal at boot | Rotary Encoder / Touch | Rotary Encoder |  |  | 3,3V | ADC2 | ja | 14 | OK | OK | outputs PWM signal at boot
15 | OK | OK | outputs PWM signal at boot | Rotary Encoder / Touch | Rotary Encoder |  |  |  | ADC2 | ja | 15 | OK | OK | outputs PWM signal at boot
16 | OK | OK |  | Temp. Sensor | TSIC 306 TO92 | GND |  | 3,3V |  | ja | 16 | OK | OK
17 | OK | OK |  | Pumpe | SSR/Relais (SSR bevorzugt) | GND | 5V | 3,3V |  | ja | 17 | OK | OK
18 | OK | OK |  | 3W-Ventil | SSR/Relais (SSR bevorzugt) |  |  |  |  | ja | 18 | OK | OK
19 | OK | OK |  | Heizung | SSR 20A | GND |  |  |  | ja | 19 | OK | OK
21 | OK | OK | SDA | Display / Touch | SDA | GND | 5V |  |  | ja | 21 | OK | OK | SDA
22 | OK | OK | SCL | Display / Touch | SCL |  |  |  |  | ja | 22 | OK | OK | SCL
23 | OK | OK |  | Flowmeter | Digimesa 932-9521-b | GND | 5V | 3,3V |  | ja | 23 | OK | OK
25 | OK | OK |  | E-Trigger | Relais | GND | 5V | 3,3V | ADC2 | ja | 25 | OK | OK
26 | OK | OK |  | Pumpe | Dimmer RobotDyn 6970622932550 |  |  |  | ADC2 | ja | 26 | OK | OK
27 | OK | OK |  | Touch | 2.8 TFT Touch Screen ILI9341Type |  |  |  | ADC2 | ja | 27 | OK | OK
32 | OK | OK |  | Waage | HX711 CLK | GND | 5V |  | ADC1 (Wifi-Input) | ja | 32 | OK | OK
33 | OK | OK |  | Waage | HX711 DAT |  |  | 3,3V | ADC1 (Wifi-Input) | ja | 33 | OK | OK
34 | OK |  | input only - no PWM | Freier GIPO |  | GND |  | 3,3V | ADC1 (Wifi-Input) | ja | 34 | OK |  | input only
35 | OK |  | input only - no PWM | Brühschalter | Schalter | GND |  | 3,3V | ADC1 (Wifi-Input) | ja | 35 | OK |  | input only
36 | OK |  | input only - no PWM | Drucksensor | Druckzelle |  |  |  | ADC1 (Wifi-Input) | ja | 36 | OK |  | input only
39 | OK |  | input only - no PWM | Freier ADC |  |  |  |  | ADC1 (Wifi-Input) | ja | 39 | OK |  | input only
EN |  |  |  | Touch | 2.8 TFT Touch Screen ILI9341Type
Quellen:
ESP32 - GPIO und Anschlussbeschreibungen (https://randomnerdtutorials.com/esp32-pinout-reference-gpios/)
 |  | Touch
 |  | PIN 1
 |  | PIN 2
 |  | PIN 3
 |  | PIN 4
 |  | PIN 5
 |  | PIN 6
 |  | RST | 3V3
 |  | VCC | 5V
 |  | GND

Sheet: BOM
BOM Export
ID | Name | Designator | Footprint | Quantity | Manufacturer Part | Manufacturer | Supplier | Supplier Part | Price | LCSC Assembly | Paste Type
1 | 220uF | C1,C2 | CAP-TH_BD6.3-P2.50-D1.0-FD | 2 | KF0J221ME050A00CV0 | Changzhou Huawei Elec | LCSC | C271304 | 0.0248 | Yes
2 | 100nF | C3,C4,C5,C6 | CAP-TH_L8.5-W5.0-P5.00-D1.2 | 4 | CT4-0805B104K500F3 | FH | LCSC | C84772 | 0.0141 | Yes
3 | E-Trigger | CN1 | CONN-TH_4P-P2.00_PH--4AW | 1 | PH-4AW | BOOMELE | LCSC | C10401 | 0.0085 | Yes | expand
4 | Heizung | CN2 | CONN-TH_PH-2AW | 1 | PH-2AW | CAX | LCSC | C722769 | 0.003545 | Yes | expand
5 | Pumpe/Ventil | CN3,CN15 | CONN-TH_6P-P2.00_PH-6AW | 2 | PH-6AW | BOOMELE | LCSC | C5662 | 0.0126 | Yes | expand
6 | Drucksensor | CN4 | CONN-TH_3P-P2.00_PH-3AK | 1 | PH-3A | Boom Precision Elec | LCSC | C146083 | 0.0108 | Yes | expand
7 | Dampfschalter | CN5 | CONN-TH_3P-P2.00_PH-3AK | 1 | PH-3A | Boom Precision Elec | LCSC | C146083 | 0.0108 | Yes | expand
8 | TSIC | CN6 | CONN-TH_PH-3AW | 1 | PH-3AW | BOOMELE | LCSC | C10400 | 0.0064 | Yes | expand
9 | Display/Touch | CN7 | CONN-TH_PH-5AW | 1 | PH-5AW | BOOMELE | LCSC | C10402 | 0.0105 | Yes | expand
10 | Waage | CN9 | CONN-TH_PH-5AW | 1 | PH-5AW | BOOMELE | LCSC | C10402 | 0.0105 | Yes | expand
11 | 5 Volt input | CN10 | CONN-TH_PH-2AW | 1 | PH-2AW | CAX | LCSC | C722769 | 0.003545 | Yes | expand
12 | Encoder/Touch | CN11 | CONN-TH_PH-5AW | 1 | PH-5AW | BOOMELE | LCSC | C10402 | 0.0105 | Yes | expand
13 | Flowmeter | CN12 | CONN-TH_4P-P2.00_PH-4AK | 1 | PH-4A | Boom Precision Elec | LCSC | C146084 | 0.0126 | Yes | expand
14 | IC2 | CN13 | CONN-TH_4P-P2.00_PH-4AK | 1 | PH-4A | Boom Precision Elec | LCSC | C146084 | 0.0126 | Yes | expand
15 | Brühschalter | CN14 | CONN-TH_3P-P2.00_PH-3AK | 1 | PH-3A | Boom Precision Elec | LCSC | C146083 | 0.0108 | Yes | expand
16 | Header-Female-2.54_1x20 | P4,P5 | HDR-TH_20P-P2.54-V-F | 2 | 2.54mm 1*20P Female header | BOOMELE | LCSC | C50984 | 0.1184 | Yes | expand
17 | 51K | R1,R2 | RES-TH_BD2.4-L6.3-P10.30-D0.6 | 2 | RD 1/4W 51K J T/B A1 | TyoHM | LCSC | C433709 | 0.00561 | Yes | expand
18 | 4.7K | R5,R6 | RES-TH_BD2.2-L6.5-P10.50-D0.6 | 2 | CFR0W4J0472A50 | UniOhm | LCSC | C61297 | 0.0055 | Yes | expand
19 | A2541WV-2X2P | V_CN13_CN7 | HDR-TH_4P-P2.54-V-R2-C2-S2.54_A2541WV-2X2P | 1 | A2541WV-2x2P | Changjiang Connectors | LCSC | C225517 | 0.0755 | Yes | expand
Bestellung
Summe | LCSC Part Number | Beschreibung | Summe2 | x | Bestellt LSCS | Prüfung
30 | C271304 | 220uF | 15 | 2 | 30 | FALSE
60 | C84772 | 100nF | 15 | 4 | 60 | FALSE
30 | C5662 | PH-6AW | 15 | 2 | 50 | FALSE
45 | C10402 | PH-5AW | 15 | 3 | 50 | FALSE
15 | C10401 | PH-4AW | 15 | 1 | 50 | FALSE
15 | C10400 | PH-3AW | 15 | 1 | 50 | FALSE
30 | C722769 | PH-2AW | 15 | 2 | 50 | FALSE
30 | C33478 | PH-6A | 15 | 2 | 50 | FALSE
45 | C2322 | PH-5A | 15 | 3 | 50 | FALSE
45 | C146084 | PH-4A | 15 | 3 | 50 | FALSE
60 | C146083 | PH-3A | 15 | 4 | 100 | FALSE
30 | C2319 | PH-2A | 15 | 2 | 50 | FALSE
30 | C50984 | 2.54mm 1*20P Female header | 15 | 2 | 30 | FALSE
30 | C433709 | 51 K | 15 | 2 | 50 | FALSE
30 | C61297 | 4,7 k | 15 | 2 | 50 | FALSE
15 | C225517 | 2x2 Header | 15 | 1 | 15 | FALSE
30 | C157952 | Housing PH 6 | 15 | 2 | 40 | FALSE
45 | C157953 | Housing PH 5 | 15 | 3 | 50 | FALSE
45 | C111514 | Housing PH 4 | 15 | 3 | 50 | FALSE
60 | C157954 | Housing PH 3 | 15 | 4 | 100 | FALSE
30 | C157955 | Housing PH 2 | 15 | 2 | 50 | FALSE
900 | C8875 | Crimptkontakte | 15 | 60 | 900 | FALSE
15 | C2689176 | Brücken | 15 | 1 | 50 | FALSE

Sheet: Datenblaetter
Einkaufsliste
 |  |  | Datenblatt
Flowmeter | Digimesa | 932-9521-b | https://www.digmesa.com/wp-content/uploads/932-952x_Bxxx_D_20V-2.pdf
Paddle | Alps Alpine | RSA0N11S9002 | https://docs.rs-online.com/453e/0900766b80124572.pdf
SSR 25A | Jotta,
SSR 2x2A | China mit Omron

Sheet: NodeMCUDev4C_Lochraster
Platinenlayout Oberseite |  |  |  |  |  |  |  |  |  |  |  |  |  |  |  |  |  |  |  |  |  |  |  |  |  |  |  |  |  |  |  | Platinenlayout Unterseite
 | A | B | C | D | E | F | G | H | I | J | K | L | M | N | O | P | Q | R | S | T | U | V | W | X | Y | Z | A | B | C | D | E |  | A | B | C | D | E | F | G | H | I | J | K | L | M | N | O | P | Q | R | S | T | U | V | W | X | Y | Z
A |  |  |  |  |  |  |  |  |  |  |  |  |  |  |  |  |  |  |  |  |  |  |  |  |  |  |  |  |  |  |  | A
B |  |  |  |  |  |  |  |  |  |  |  |  |  |  |  |  |  |  |  |  |  |  |  |  |  |  |  |  |  |  |  | B
C |  |  |  |  |  |  |  |  |  |  |  |  |  |  |  |  |  |  |  |  |  |  |  |  |  |  |  |  |  |  |  | C
D |  |  |  |  |  |  |  |  |  |  |  |  |  |  |  |  |  |  |  |  |  |  |  |  |  |  |  |  |  |  |  | D
E |  |  |  |  |  |  |  |  |  |  |  |  |  |  |  |  |  |  |  |  |  |  |  |  |  |  |  |  |  |  |  | E
F |  |  |  |  |  |  |  |  |  |  |  |  |  |  |  |  |  |  |  |  |  |  |  |  |  |  |  |  |  |  |  | F
G |  |  |  |  |  |  |  |  |  |  |  |  |  |  |  |  |  |  |  |  |  |  |  |  |  |  |  |  |  |  |  | G
H |  |  |  |  |  |  |  |  | o | o | o | o | o | o | o | o | o | o | o | o | o | o | o | o | o | o | o |  |  |  |  | H |  |  |  |  | o | o | o | o | o | o | o | o | o | o | o | o | o | o | o | o | o | o | o
I |  |  |  |  |  |  |  |  | 5V | 11 | 10 | 9 | 13 | GND | 12 | 14 | 27 | 26 | 25 | 33 | 32 | 35 | 34 | 39 | 36 | EN | 3.3 |  |  |  |  | I |  |  |  |  | 3.3 | EN | 36 | 39 | 34 | 35 | 32 | 33 | 25 | 26 | 27 | 14 | 12 | GND | 13 | 9 | 10 | 11 | 5V
J |  |  |  |  |  |  |  |  |  |  |  |  |  |  |  |  |  |  |  |  |  |  |  |  |  |  |  |  |  |  |  | J
K |  |  |  |  |  |  |  |  |  |  |  |  |  |  |  |  |  |  |  |  |  |  |  |  |  |  |  |  |  |  |  | K
L |  |  |  |  |  |  |  |  |  |  |  |  |  |  |  |  |  |  |  |  |  |  |  |  |  |  |  |  |  |  |  | L
M |  |  |  |  |  |  |  |  |  |  |  |  |  |  |  |  |  |  |  |  |  |  |  |  |  |  |  |  |  |  |  | M
N |  |  |  |  |  |  |  |  |  |  |  |  |  |  |  |  |  |  |  |  |  |  |  |  |  |  |  |  |  |  |  | N
O |  |  |  |  |  |  |  |  |  |  |  |  |  |  |  |  |  |  |  |  |  |  |  |  |  |  |  |  |  |  |  | O
P |  |  |  |  |  |  |  |  |  |  |  |  |  |  |  |  |  |  |  |  |  |  |  |  |  |  |  |  |  |  |  | P
Q |  |  |  |  |  |  |  |  | 6 | 7 | 8 | 15 | 2 | 0 | 4 | 16 | 17 | 5 | 18 | 19 | GND | 21 | 3 | 1 | 22 | 23 | GND |  |  |  |  | Q |  |  |  |  | GND | 23 | 22 | 1 | 3 | 21 | GND | 19 | 18 | 5 | 17 | 16 | 4 | 0 | 2 | 15 | 8 | 7 | 6
R |  |  |  |  |  |  |  |  | o | o | o | o | o | o | o | o | o | o | o | o | o | o | o | o | o | o | o |  |  |  |  | R |  |  |  |  | o | o | o | o | o | o | o | o | o | o | o | o | o | o | o | o | o | o | o
S |  |  |  |  |  |  |  |  |  |  |  |  |  |  |  |  |  |  |  |  |  |  |  |  |  |  |  |  |  |  |  | S
T |  |  |  |  |  |  |  |  |  |  |  |  |  |  |  |  |  |  |  |  |  |  |  |  |  |  |  |  |  |  |  | T
U |  |  |  |  |  |  |  |  |  |  |  |  |  |  |  |  |  |  |  |  |  |  |  |  |  |  |  |  |  |  |  | U
V |  |  |  |  |  |  |  |  |  |  |  |  |  |  |  |  |  |  |  |  |  |  |  |  |  |  |  |  |  |  |  | V
W |  |  |  |  |  |  |  |  |  |  |  |  |  |  |  |  |  |  |  |  |  |  |  |  |  |  |  |  |  |  |  | W
X |  |  |  |  |  |  |  |  |  |  |  |  |  |  |  |  |  |  |  |  |  |  |  |  |  |  |  |  |  |  |  | X
Y |  |  |  |  |  |  |  |  |  |  |  |  |  |  |  |  |  |  |  |  |  |  |  |  |  |  |  |  |  |  |  | Y
Z |  |  |  |  |  |  |  |  |  |  |  |  |  |  |  |  |  |  |  |  |  |  |  |  |  |  |  |  |  |  |  | Z
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

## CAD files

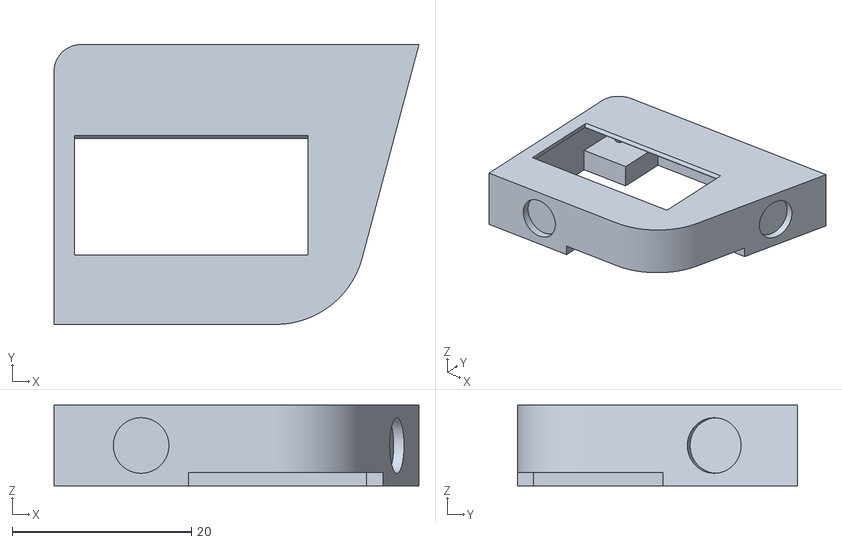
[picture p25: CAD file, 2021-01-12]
3d-designs/Case Gaggia.stl
40.7 x 31.2 x 9.00

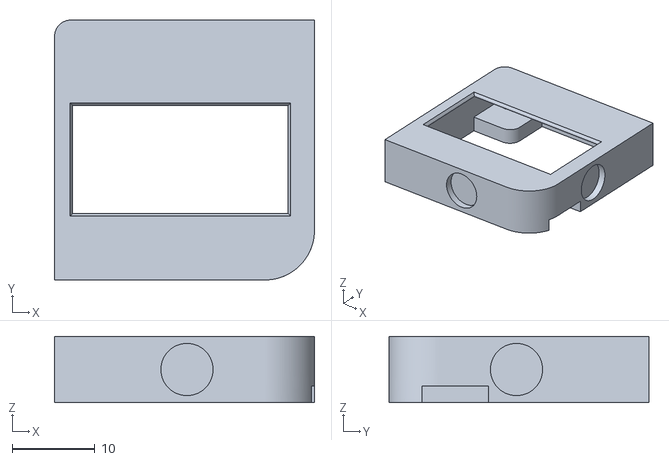
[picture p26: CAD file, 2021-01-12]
3d-designs/Case Rancilio.stl
31.4 x 31.4 x 8.00

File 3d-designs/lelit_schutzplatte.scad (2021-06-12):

use <MCAD/triangles.scad>;

inner_wall_height = 190;

wall_thickness = 1.5;

horizontal_piece_depth = 35;

front_wall_height = 12;

width = 190;

screw_diameter = 4;

screw_offset = 7;

screw_piece_width = 15;

translate([screw_piece_width, horizontal_piece_depth + wall_thickness*2,wall_thickness]) rotate([180,90,90]) triangle(front_wall_height * 1.1,front_wall_height + wall_thickness,wall_thickness);

translate([width - screw_piece_width, horizontal_piece_depth + wall_thickness,wall_thickness]) rotate([0,90,90]) triangle(front_wall_height * 1.1,front_wall_height + wall_thickness,wall_thickness);


// large inner wall
cube([width, wall_thickness, inner_wall_height]);

// horizontal piece
translate([0, wall_thickness, 0]) cube([width, horizontal_piece_depth, wall_thickness]);

// pieces connecting to the screws
difference()
{
    translate([0, wall_thickness + horizontal_piece_depth, - (front_wall_height)]) cube([screw_piece_width, wall_thickness, front_wall_height + wall_thickness]);
    
    translate([screw_offset, horizontal_piece_depth + wall_thickness / 2, -front_wall_height/2]) rotate(a=[0,90,90]) cylinder(h = 10 * wall_thickness, r = screw_diameter / 2, $fn=50, center = true);

}

difference()
{
    translate([width - screw_piece_width, wall_thickness + horizontal_piece_depth, - (front_wall_height)]) cube([screw_piece_width, wall_thickness, front_wall_height + wall_thickness]);
    translate([width - screw_offset, horizontal_piece_depth + wall_thickness / 2, -front_wall_height/2]) rotate(a=[0,90,90]) cylinder(h = 10 * wall_thickness, r = screw_diameter / 2, $fn=50, center = true);
}

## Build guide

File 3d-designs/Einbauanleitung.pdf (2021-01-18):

# Schritt 1

## Pins vom Display kürzen

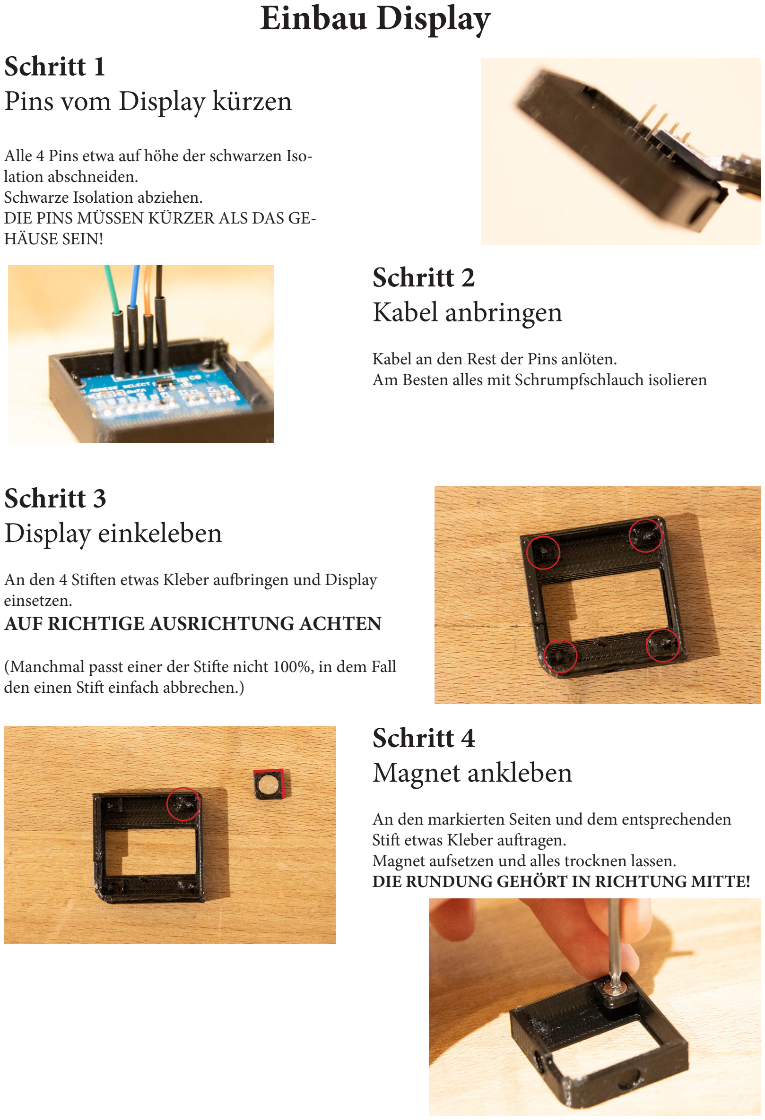
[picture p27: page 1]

Alle 4 Pins etwa auf höhe der schwarzen Isolation abschneiden.
Schwarze Isolation abziehen.
DIE PINS MÜSSEN KÜRZER ALS DAS GE-HÄUSE SEIN!

# Schritt 2

## Kabel anbringen

Kabel an den Rest der Pins anlöten.
Am Besten alles mit Schrumpfschlauch isolieren

# Schritt 3

## Display einkeleben

An den 4 Stiften etwas Kleber aufbringen und Display einsetzen.

### AUF RICHTIGE AUSRICHTUNG ACHTEN

(Manchmal passt einer der Stifte nicht 100%, in dem Fall den einen Stift einfach abbrechen.)

# Schritt 4

## Magnet ankleben

An den markierten Seiten und dem entsprechenden Stift etwas Kleber auftragen.
Magnet aufsetzen und alles trocknen lassen.
DIE RUNDUNG GEHÖRT IN RICHTUNG MITTE!

# Einbau Display

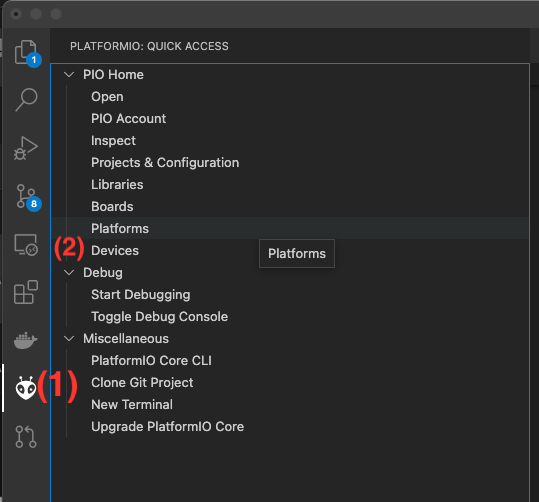
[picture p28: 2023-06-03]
img/softwareinstall/swinstall7.png

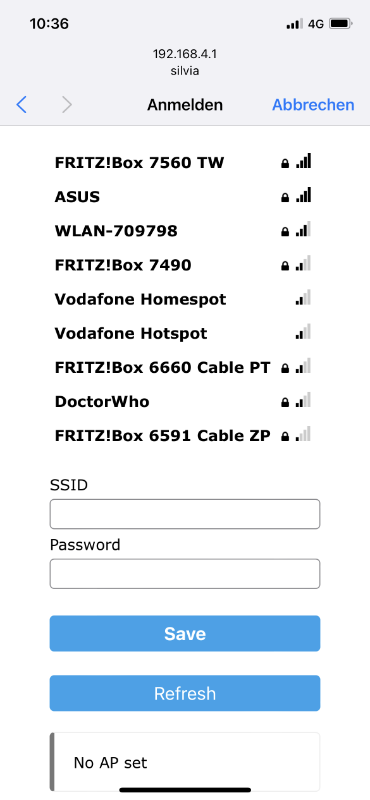
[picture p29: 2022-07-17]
img/wlan-setup3.PNG

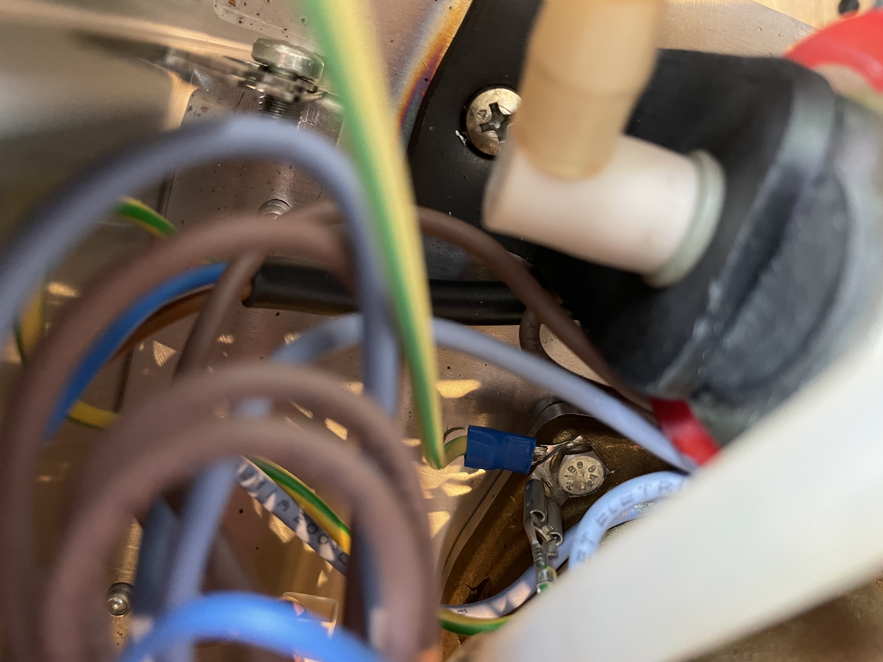
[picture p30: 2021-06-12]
img/bauanleitungen/lelit-pl41em/IMG_1462.jpeg

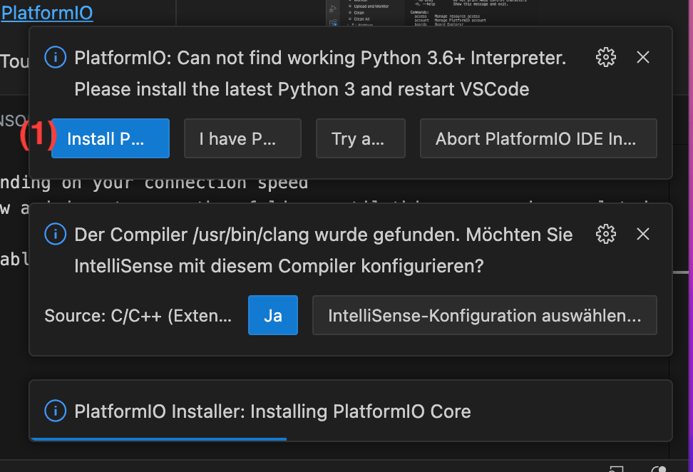
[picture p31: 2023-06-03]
img/softwareinstall/swinstall2.png

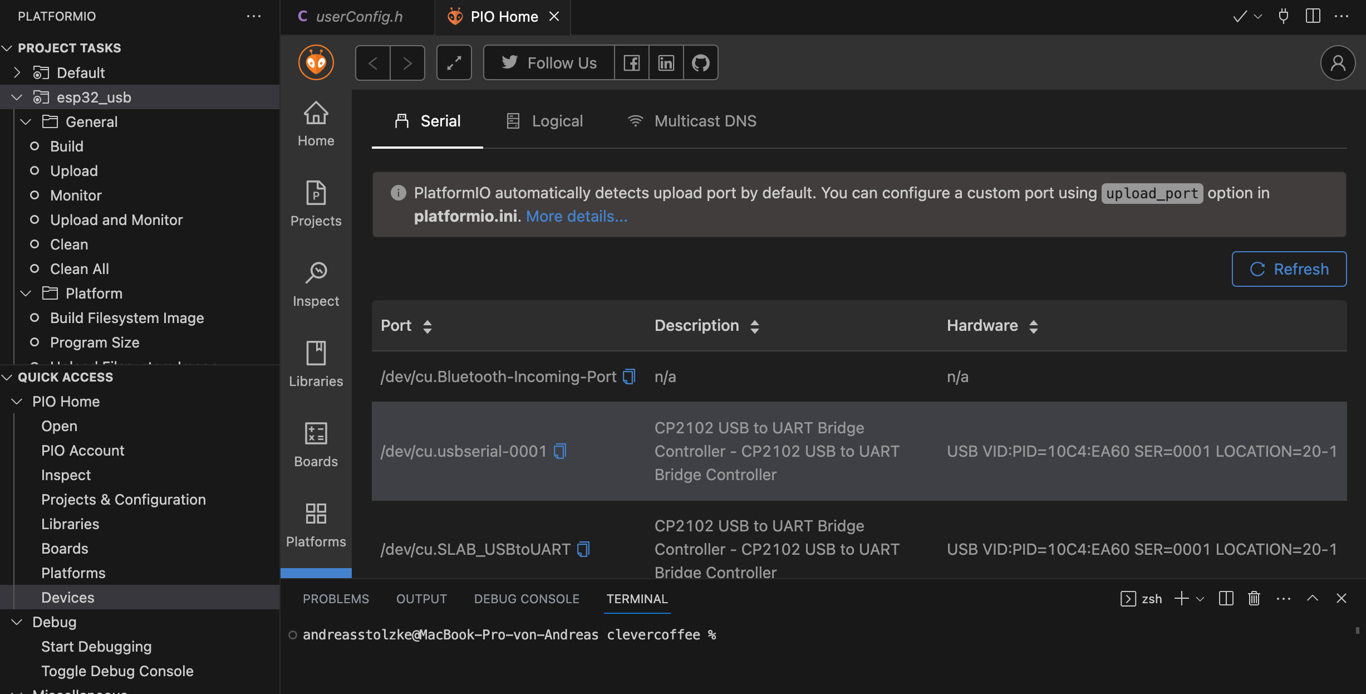
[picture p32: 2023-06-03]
img/softwareinstall/swinstall8.png

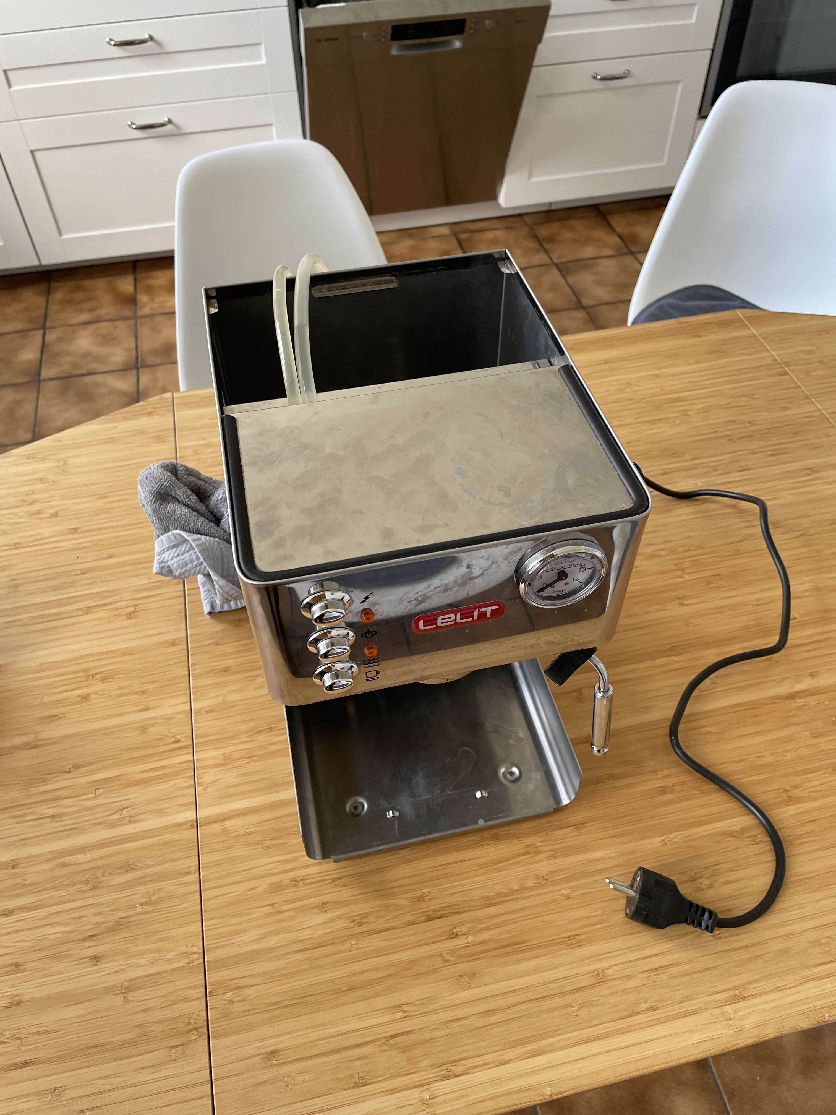
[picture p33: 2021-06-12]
img/bauanleitungen/lelit-pl41em/IMG_1451.jpeg

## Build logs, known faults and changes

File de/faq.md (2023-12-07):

---
layout: default
title: FAQ
parent: DE - Handbuch
has_children: false
nav_order: 8
---

# FAQ

Frage: Auf dem Display erscheint eine „emergency stop“ Warnung ab 120°C, warum?

> Die Notabschaltung greift ab 120°C, um ein Überhitzen der Maschine durch unvorhergesehenes Reglerverhalten zu vermeiden. Ab einer Temperatur <100°C wird die Notabschaltung wieder außer Kraft gesetzt. Während des Dampfbezuges erscheint diese Meldung regelmäßig (da mehr als 120°C), hat allerdings keinen Einfluss, da der Dampf nicht über den Regler gesteuert wird.

Frage: Warum schaltet der Heizungs-SSR nicht?

> Häufig passiert es, dass der Signal des Pins nicht am + Pol sondern – Pol des SSRs angeschlossen ist. Bitte prüft, ob ihr richtig den SSR angeschlossen habt. Mit einem Messgerät kann man den Durchgang bei einem SSR nicht prüfen. Höchstens, ob die gewünschten 3,3 Volt am SSR anliegen.

Frage: Meine PID-Werte passen nicht, meine Maschine schwingt über o.ä.

> Schaut bitte zu erst in unsere PID-Wert Liste [PID-Werte](./customization/pid-werte.md) oder ab Version 3.0.1 [PID-Werte](./customization/pid-werte.md), hier sind für viele PID-Werte dokumentiert für den Kaltstart, den normalen Betrieb und für die Brüherkennung. Bei Fragen im Chat bitte genau sagen, was genau nicht passt und schickt am besten Werte aus eurem Blynk dazu. Am besten im jeweiligen Chat zu den Maschinen.

Frage: Kann ich mein Iphone oder Apple Watch nutzen um z.B. den Dampfmodus zu aktivieren.
> Ja, kannst du. Der User [@saway](https://github.com/sway) hat hierzu ein Kurzbefehl gebaut, womit du via Apple Watch oder Iphone den Steam mode aktivieren kannst. Der Link zum Kurzbefehl (muss auf dem Iphone geöffnet werden): [Kurzbefehl](https://www.icloud.com/shortcuts/ee08f4989e834fecb03d96d7f3d08425) Ihr müsst nur die IP von eurer Maschine dort eintragen. (fixe IP vorrausgesetzt)

Frage: Das Display zeigt an: "PID is disabled manually"
> Wenn du das erste mal deinen PID in Betrieb nimmst, musst du die vom ESP gehostete Webseite öffnen und die PID auf der Parameter Seite aktivieren.

Frage: Mein ESP8266 startet nicht korrekt den Access Point, um mein Wlan einzurichten. Was soll ich tun? 
> Leider kollidiert der Wifi Manager und das Display bei der Ersteinrichtung. Beim ESP32 ist dieses Problem nicht vorhanden. In Release 3.3.0 haben wir den Wifimanger für den ESP8266 entfernt. Wir empfehlen ein Update auf diese Version, dort werden die Wifi Zugangsdaten wieder in der userconfig.h fest eingetragen.

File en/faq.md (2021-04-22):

---
layout: default
title: FAQ
parent: EN - Manual
has_children: false
nav_order: 7
---

# FAQ

Question: The warning „emergency stop“ appears on the display at 120°C, why?

> The emergency shutdown kicks in at 120 °C in order to prevent overheating of the machine, which caused by onforseen behaviour of the software or hardware. After the temperature has dropped below 100 °C, the PID will resume normal operation. When in steam mode, this message will apear regulary (temp. above 120 °C), but doesn't influence the function of the machine since steam is not controlled by the PID.  

Question: why does the heating SSR not function properly?

> A common mistake is that the signal pin is not connected to "+", but to the "-" connector of the SSR. Please double check if you have connected the SSR correctly

Question: My PID values don't seem to work, e.g. the temperature overshoots

> Please have a look at our PID-value list [PID-values](../de/customization/pid-werte.md), where many working values are listed for cold-start, normal operation and brew-detection. In case you want to ask for help in the chat, please explain the exact problem (best would be to also send the values from Blynk).

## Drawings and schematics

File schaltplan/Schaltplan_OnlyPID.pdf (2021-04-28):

# www.rancilio-pid.de https://github.com/rancilio-pid

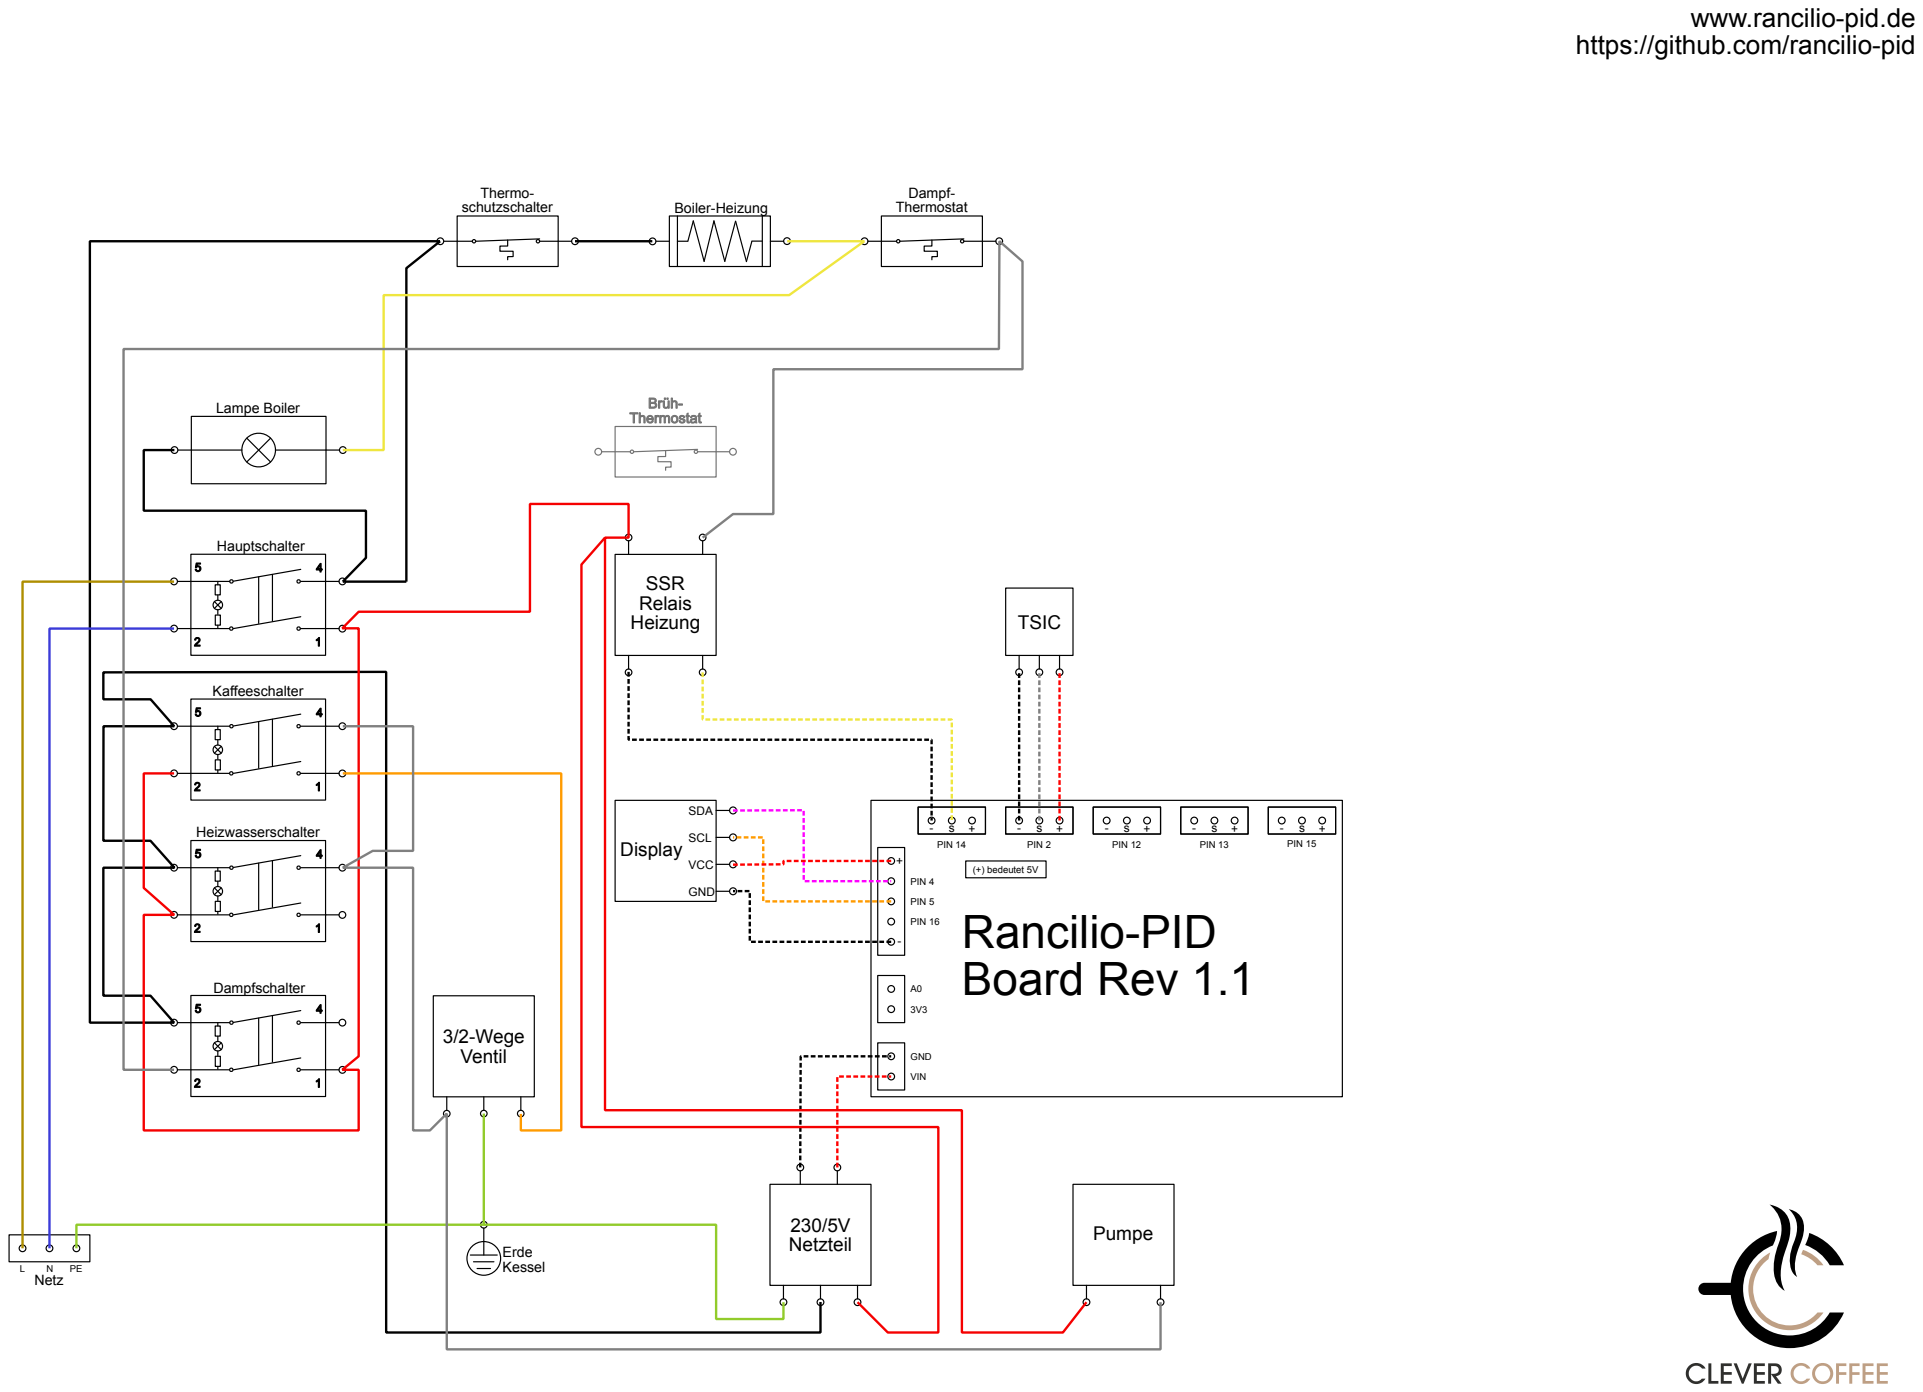
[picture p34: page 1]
Lampe Boiler; Thermo- schutzschalter; Dampf- Thermostat; Brüh- Thermostat; Hauptschalter; Kaffeeschalter; Heizwasserschalter; Dampfschalter; Boiler-Heizung; SSR Relais Heizung; 3/2-Wege Ventil; Netzteil; Pumpe; Display; SDA; SCL; VCC; GND; TSIC; + - Rancilio-PID Board Rev 1.1; PIN 4; PIN 14; PIN 2; PIN 12; PIN 13; PIN 15; PIN 5; PIN 16; VIN; (+) bedeutet 5V; Erde; Kessel; Netz

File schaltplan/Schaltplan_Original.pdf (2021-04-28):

# www.rancilio-pid.de https://github.com/rancilio-pid

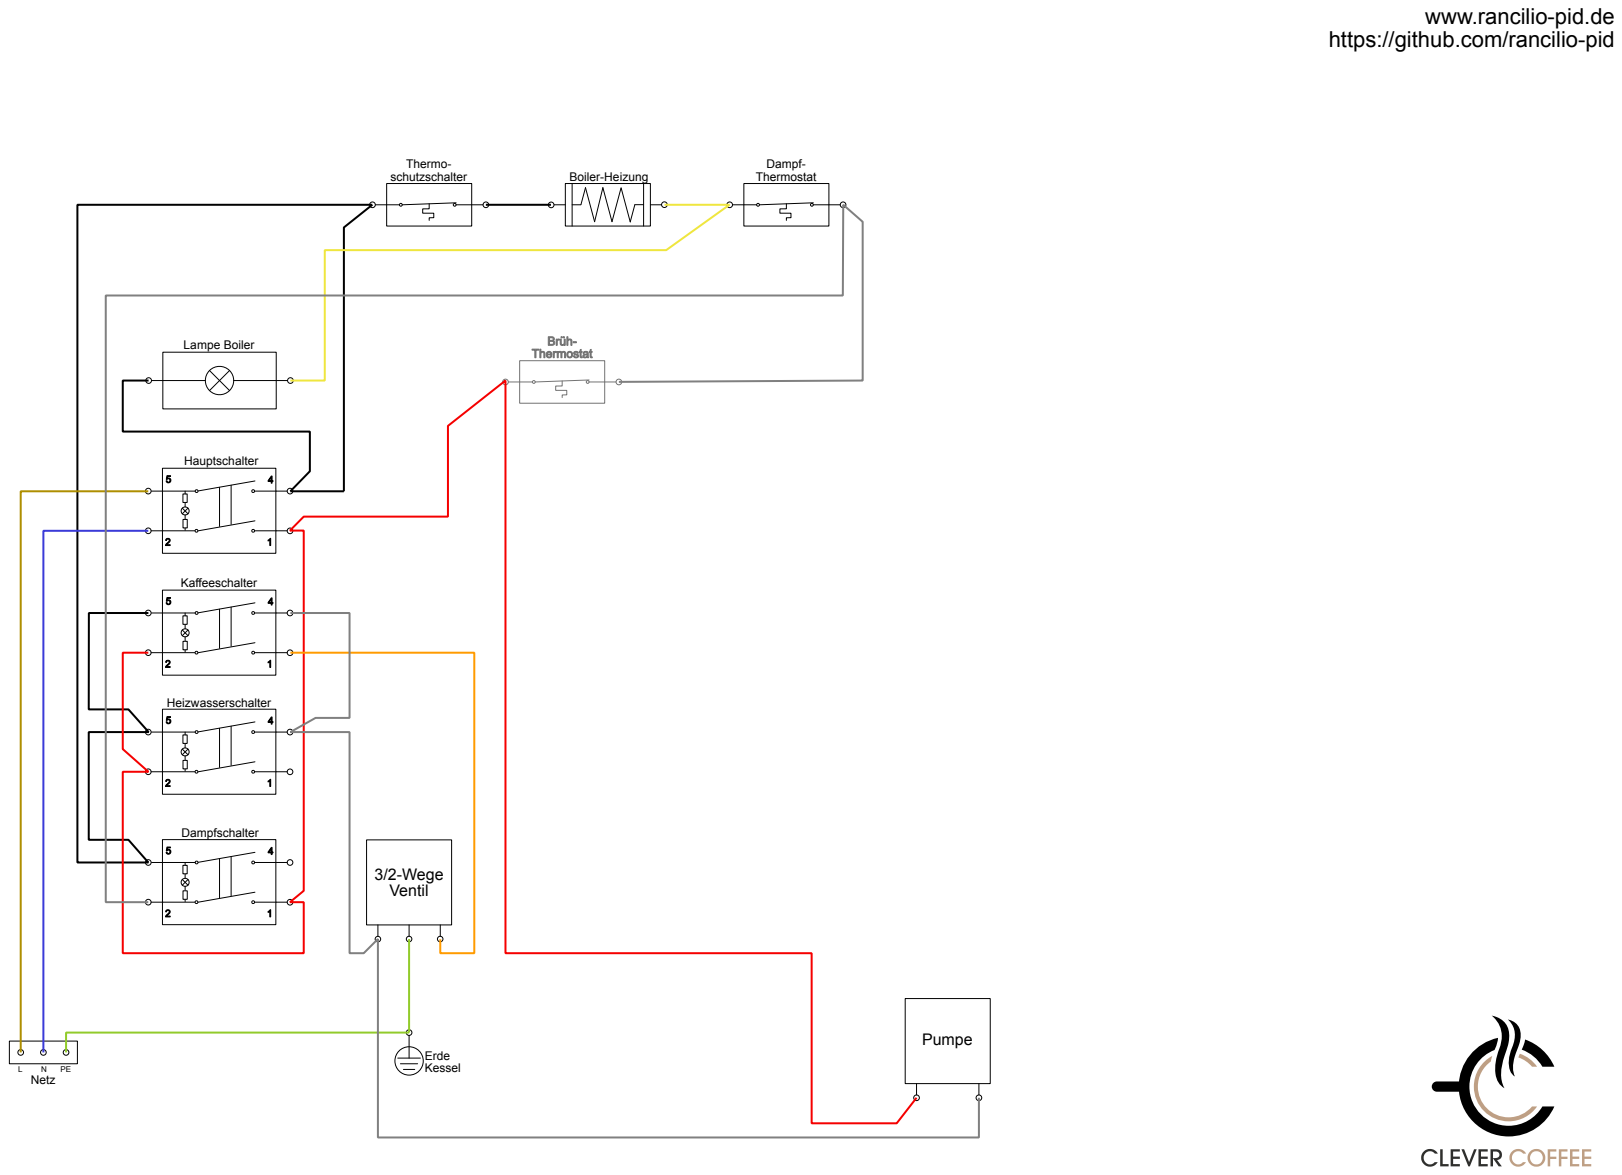
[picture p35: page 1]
Lampe Boiler; Thermo- schutzschalter; Dampf- Thermostat; Brüh- Thermostat; Hauptschalter; Kaffeeschalter; Heizwasserschalter; Dampfschalter; Boiler-Heizung; 3/2-Wege Ventil; Pumpe; Erde; Kessel; Netz

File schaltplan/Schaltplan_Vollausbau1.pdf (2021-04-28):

## Relais Pumpe

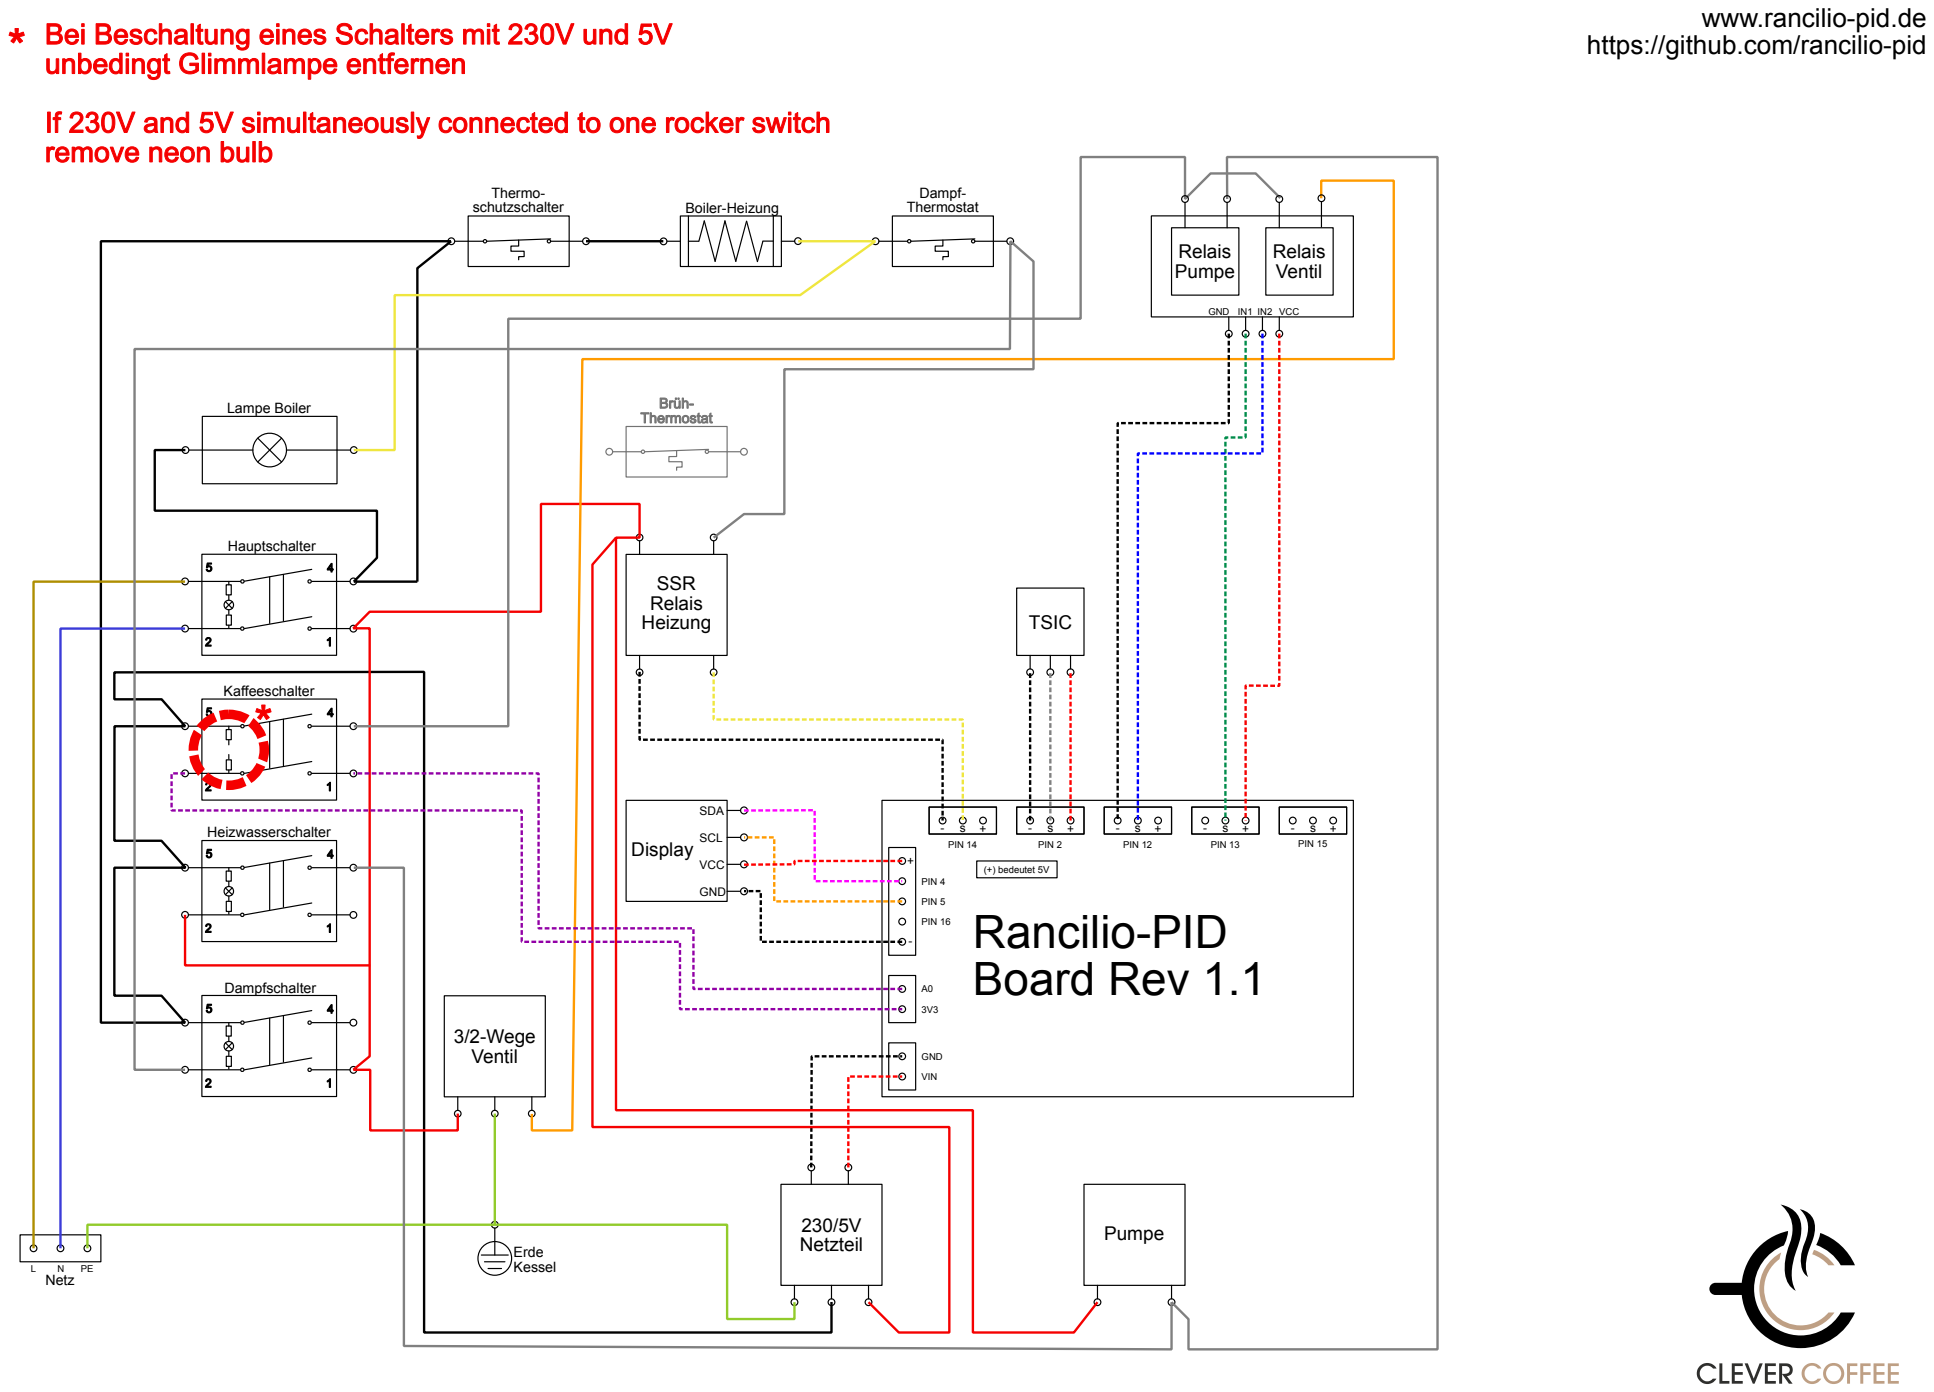
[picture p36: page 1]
Lampe Boiler; Thermo- schutzschalter; Dampf- Thermostat; Brüh- Thermostat; Hauptschalter; Kaffeeschalter; Heizwasserschalter; Dampfschalter; Boiler-Heizung; SSR Relais Heizung; 3/2-Wege Ventil; Netzteil; Pumpe; Display; SDA; SCL; VCC; GND; TSIC; + - Rancilio-PID Board Rev 1.1; PIN 4; PIN 14; PIN 2; PIN 12; PIN 13; PIN 15; PIN 5; PIN 16; VIN; (+) bedeutet 5V; Erde; Kessel; Netz; Relais Ventil; GND IN1 IN2 VCC

www.rancilio-pid.de

Bei Beschaltung eines Schalters mit 230V und 5V
unbedingt Glimmlampe entfernen

https://github.com/rancilio-pid

If 230V and 5V simultaneously connected to one rocker switch
remove neon bulb

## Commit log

2020-12-20 Arduino Einrichtung finalisiert
2020-12-22 blynk und erster Test
2020-12-27 bestellliste und einleitung ergänzt
2020-12-29 kaltstart werte in pid-werte
2021-01-03 Formatierung der Maschinentypen verbessert
2021-01-03 Formulierungen geändert und neuen Testing Abschnitt eingefügt
2021-01-03 Update brueherkennung.md
    Ergänzung BD PID
2021-01-03 PRB -> PCB
2021-01-03 PCB Lieferung erneut hinzugefügt
2021-01-16 Alternative Sensoren hinzugefügt
2021-01-20 neue config und ota details
2021-01-31 Hitzebeständige Kabel hinzugefügt, nicht passende M4 Ring-Kerbschuhe durch M5 und M3 ersetzt
2021-02-01 MD Tabellen korrigiert und neu sortiert
2021-03-07 add description of waterlevel sensor
2021-04-22 move programmcode.md to its own page, write a few sentences about creating userConfig.h from sample
2021-05-18 LED Umbau
2021-05-25 added needed version for esp board driver
2021-05-25 added info onn board driver version
2021-05-25 QuickMill PID-Werte & Typos
    PID-Werte für Quick Mill Thermoblock ergänzt, Tippfehler korrigiert
2021-05-25 Quick Mill im en-Manual
    Ergänzung Quick Mill im en-Manual
2021-05-29 deutsche erklärung zu Visual Studio Code und PlatformIO
2021-06-08 Update software-part-II.md
    Änderungen für MACHINEID und Typos
2021-06-09 Bauanleitung Lelit PL41EM
    [lelit_schutzplatte.scad]
2021-06-09 edit include path in openscad file
    [lelit_schutzplatte.scad]
2021-07-28 Widerstand fuer SSR und Pumpe zugefuegt
    Info zum 100k/200k Widerstand wg SSR und Rota eingefuegt. Alten Verweis auf die 230V/5V Problematik am Brewswitch aktualisiert.
2022-01-10 Added Platinendesign
    [BOM_Esp8266_4layer_rev4-3und5volt_display_20181022220223.xlsx, ESP32_DEV_BOARD_REV0_PINOUT_BOM.xlsx]
2022-02-16 close #23
    [Case Gaggia.stl, Case Rancilio.stl, lelit_schutzplatte.scad]
2022-05-17 Update thermoblock.md
    Aktualisierung der Steuerung für die Dampfmoduserkennung bei QM Thermoblockmaschinen.
2022-06-22 arduino to archive and new menu for software II
2022-10-22 index / readme updates (user CleverCoffee instead of Rancilio PID)
2022-10-22 pid parameters and some added links
2022-10-25 PV-TV-PID Aufnahme
2023-05-03 pcb esp32
2023-05-06 swinstall esp32
2023-08-13 minor fix PSU + Bugtracker PCB
2023-12-07 Update bestellliste.md
    change chat link
    adding info pcb out pf stock
2023-12-07 Update visual-studio-code.md
    fix homebrew commands
    see: https://github.com/rancilio-pid/ranciliopid-handbook/issues/43
